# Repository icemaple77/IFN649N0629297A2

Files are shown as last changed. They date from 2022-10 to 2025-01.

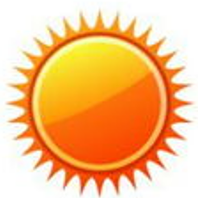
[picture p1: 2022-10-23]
layer3/client/src/img/sunny.png

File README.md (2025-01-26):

# Secure Cloud Infrastructure for Enterprise

## **Introduction**

This project mainly realized a fully automatic, unattended, green energy irrigation system. Firstly, the system is mainly divided into three layers and four modules, which are sensor layer, edge computing layer and cloud layer. The modules are data processing module, instruction management module, power management module and visualization module.

The system is powered by solar panels, and electric energy is stored into an 18650 storage battery through a 12-volt to 5-volt three-terminal voltage regulator. The sensor and MCU are powered by the battery. If the unsunny or less sunny area provides a 5V charging interface, a mobile phone charger can be used to power the entire system. The data detected by the sensor will be sent to the Raspberry PI in the middle layer, which will simply process the received data and publish the data to the AWS MQTT server for use by other clients. At the same time, a nano pi will subscribe to the data from the cloud, detect whether the data has changed, and send the latest value to the monitor for display. The watering controller controls the pump to complete the automatic irrigation according to the change of the value. This action can also be controlled by the user via an APP.

At the same time, a Web Server is set up on AWS to provide users with visual data access.

### **Keywords: MQTT, IoT, Network, Solar, Raspberry Pi, Water Pump,irrigation, Python, Arduino, Nodejs, AWS,Mosquito, Express, react， C， C++，Teensy，**

## **Example: [https://www.chenyun.org](https://www.chenyun.org/)**

## **Directory**



There are three project directories, one for each level of Code.

layer 1: Arduino Code.

layer 2: Js and python code (Python code to be perfected)

layer 3: Express Sever and React Client



The key used system directory corresponds to

Sensor

Pump

Monitor

Each directory contains the system firmware for an Arduino, and the applicable version is Teensy 2.0

The Arduino kit can be used to brush the hardware, and the link diagram is introduced later.



The Node file used in this example lives in the Node directory and is running under Node16.0. Simply execute node + file.js on a machine with a network connection.

`node Sensor.js`

`node Pump.js`

`node Monitor.js`

Make sure the teensy device has a Bluetooth connection to the device you're running the app on before executing the command.



The Server should be deployed on a Linux server with Node js 16.0 installed.

The command is

`cd Server`

`Npm install`

`npm start`

## **Architecture**









## **Design circuit diagram**

[]()

### **Sensor**



### **Pump**



Monitor



### **Technical parameters**

Sensor:

1. Rain Sensor
2. Temperature and Humidity Sensor
3. Soil moisture Sensor
4. Teensy 2.0 board
5. 18650 battery
6. switch x 2
7. Led
8. 3 Pin Socket x 2
9. Charge Board
10. 12v to 5v Regulator
11. sink
12. Bluetooth HC-05

Pump:

1. Teensy 2.0 board
2. Bluetooth HC-05
3. PNP 140 Transistor
4. Water Pump

Monitor

1. Teensy 2.0 Board
2. 0.96 LCD
3. Bluetooth HC-05

Flow Diagram



Web





<!--TLS is used to encrypt the session transmission to ensure data security.-->


Be sure to replace your own CA certificate



Link:

MQTT:

mqtt://mqtt.chenyun.org

port: 1883

Username password authentication has been enabled



## **The power supply parameters**



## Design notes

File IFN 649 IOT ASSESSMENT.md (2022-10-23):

# IFN 649 IOT ASSESSMENT

## Introduction

This project mainly realized a fully automatic, unattended, green energy irrigation system. Firstly, the system is mainly divided into three layers and four modules, which are sensor layer, edge computing layer and cloud layer. The modules are data processing module, instruction management module, power management module and visualization module.

The system is powered by solar panels, and electric energy is stored into an 18650 storage battery through a 12-volt to 5-volt three-terminal voltage regulator. The sensor and MCU are powered by the battery. If the unsunny or less sunny area provides a 5V charging interface, a mobile phone charger can be used to power the entire system. The data detected by the sensor will be sent to the Raspberry PI in the middle layer, which will simply process the received data and publish the data to the AWS MQTT server for use by other clients. At the same time, a nano pi will subscribe to the data from the cloud, detect whether the data has changed, and send the latest value to the monitor for display. The watering controller controls the pump to complete the automatic irrigation according to the change of the value. This action can also be controlled by the user via an APP.

At the same time, a Web Server is set up on AWS to provide users with visual data access.

#####  Keywords: MQTT, IoT, Network, Solar, Raspberry Pi, Water Pump,irrigation, Python, Arduino, Nodejs, AWS,Mosquito, Express, react， C， C++，Teensy，

## Example: https://www.chenyun.org

## Directory



There are three project directories, one for each level of Code.

layer 1: Arduino Code.

layer 2: Js and python code (Python code to be perfected)

layer 3: Express Sever and React Client



The key used system directory corresponds to

Sensor

Pump

Monitor

Each directory contains the system firmware for an Arduino, and the applicable version is Teensy 2.0

The Arduino kit can be used to brush the hardware, and the link diagram is introduced later.



The Node file used in this example lives in the Node directory and is running under Node16.0. Simply execute node + file.js on a machine with a network connection.

`node Sensor.js`

`node Pump.js`

`node Monitor.js`

Make sure the teensy device has a Bluetooth connection to the device you're running the app on before executing the command.



The Server should be deployed on a Linux server with Node js 16.0 installed.

The command is

`cd Server`

`Npm install`

`npm start`

## Architecture









## Design circuit diagram

### Sensor



### Pump



Monitor



### Technical parameters

Sensor:

1. Rain Sensor
2. Temperature and Humidity Sensor
3. Soil moisture Sensor
4. Teensy 2.0 board
5. 18650 battery
6. switch x 2
7. Led 
8. 3 Pin Socket x 2
9. Charge Board
10. 12v to 5v Regulator
11. sink
12. Bluetooth HC-05

Pump:

1. Teensy 2.0 board
2. Bluetooth HC-05
3. PNP 140 Transistor
4. Water Pump

Monitor

1. Teensy 2.0 Board
2. 0.96 LCD
3. Bluetooth HC-05

Flow Diagram



Web





<!--TLS is used to encrypt the session transmission to ensure data security.-->





Be sure to replace your own CA certificate

Link:

MQTT: 

mqtt://mqtt.chenyun.org

port: 1883

Username password authentication has been enabled

	

## The power supply parameters



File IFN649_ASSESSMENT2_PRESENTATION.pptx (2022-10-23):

## IFN 649 Advanced Networks Assessment2 Smart watering system

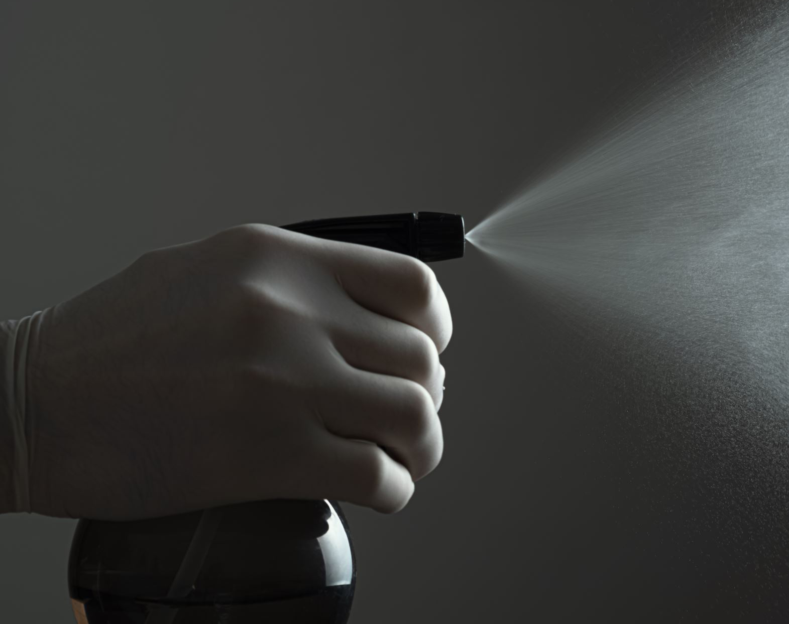
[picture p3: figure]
Hand spraying sanitiser

Lecturers: Prof Raja Jurdak
Dr. Gowri Ramachandran
Tutor name: Jun Wook Heo
Student ID： N10629297
Student Name： Chen Yun（Michael）

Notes:
For the project I‘m going talk about smart watering system

## Description of project

d

Tier 1： outdoor

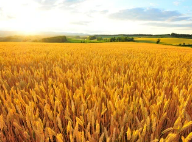
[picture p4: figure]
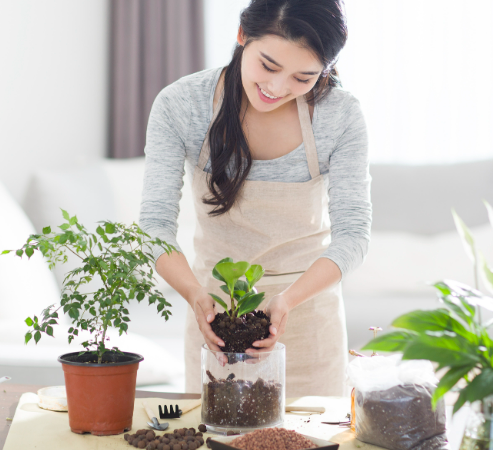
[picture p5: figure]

Internet

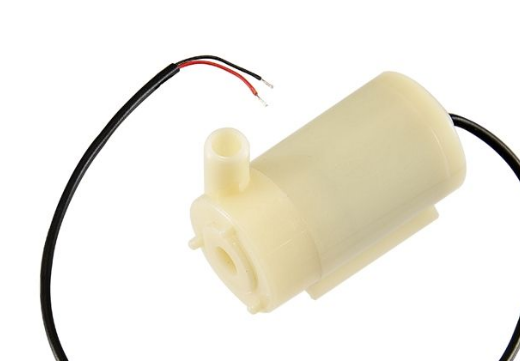
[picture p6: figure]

MCU

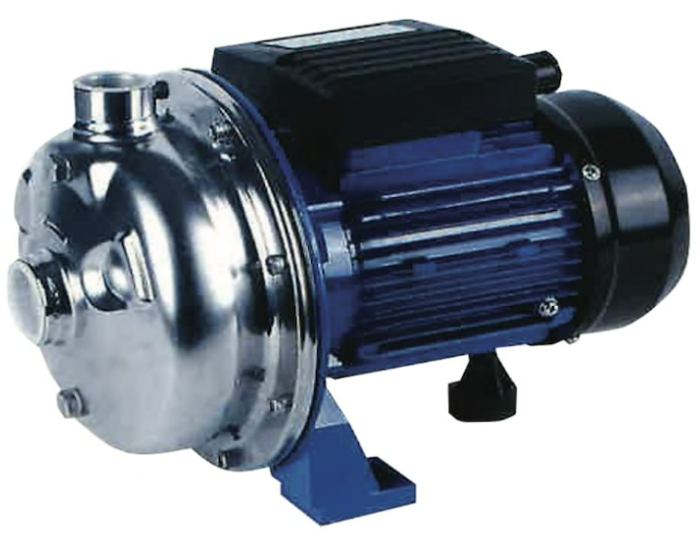
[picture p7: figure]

Tier 2

Essential: MQTT Server

Optional: Web Service

Tier 3

Rain sensor

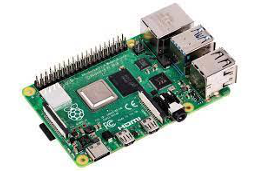
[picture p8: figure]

MCU

Temperature sensor

Soil moisture sensor

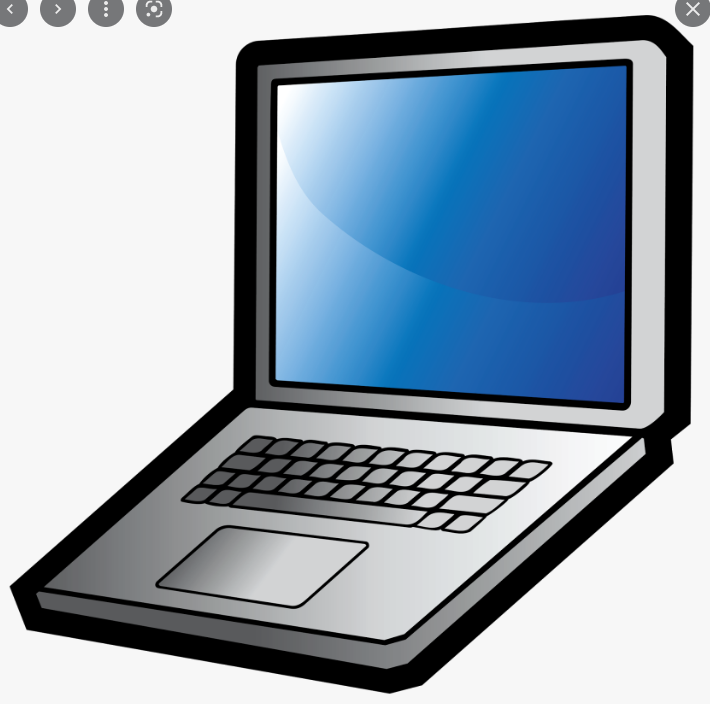
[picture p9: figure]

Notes: This project is mainly to address a problem of watering plants.
Different plants have different water requirements, and either leaving the water or overwatering will lead to the death of the plant.
And watering plants in hot or cold weather could lead to unhealthy for them
So using this system can help us to water the plants automatically.
As this diagram, the system include 3 layers.
Firstly, MCU is used to control some sensors in the first layer.
these sensors are mainly responsible for collect moisture data of soil, monitor the temperature of the environment and detect whether when it is raining.

the MCU is responsible for forwarding data to the second layer, or receiving order from the Raspberry PI to control the watering pump.

Next talk about the second layer, Raspberry PI exchanges data with first layer via Bluetooth.
At the here, I consider using wifi to replace Bluetooth, because WIFI can increase the distance and improve stability for transmission .
MQTT service will be used in this system . It is responsible to subscribe and publish data for Raspberry PI.
In addition, if I have enough time, I will build a web service based Nodejs to display the data on the web.
The detailed working principle of each layer will be introduced later.
。
The system can be used in many scenarios . For example, it can help farmers to water farm automatic.
Or at home it also can be used to water plant in the yard.
It can help people to save time and save water. The important is that it can keep the plants living healthy
Next, I will talk about each layer how does it work

## Sensor layer

Tier 2

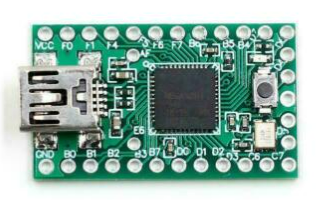
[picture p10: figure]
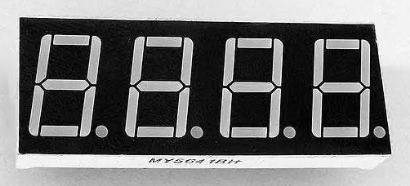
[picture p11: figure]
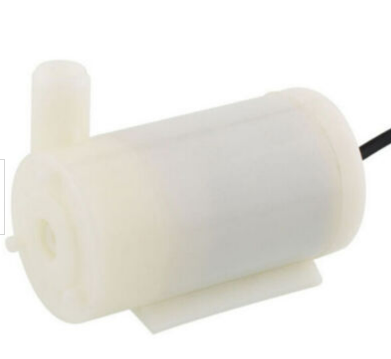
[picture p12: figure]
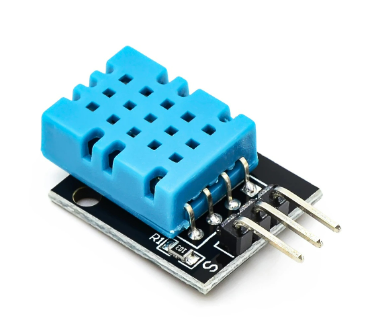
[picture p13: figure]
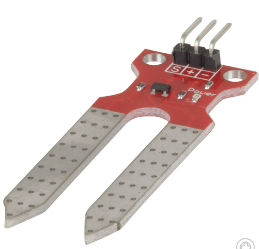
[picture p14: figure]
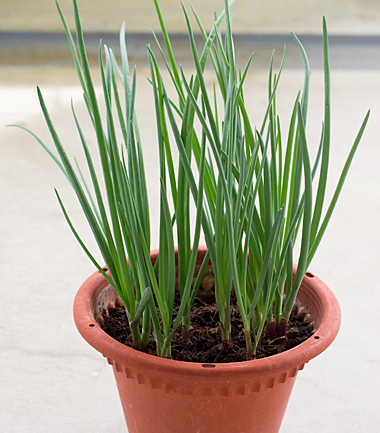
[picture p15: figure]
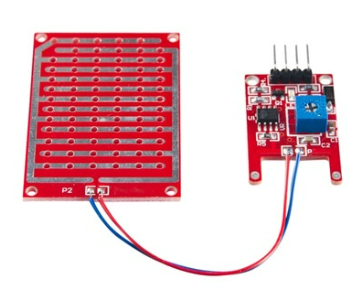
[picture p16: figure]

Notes: The first layer is sensor layer
There are three sensors used here and a water pump
The value of moisture will be got through the soil sensor
The rain sensor detects if it’s raining
The temperature sensor get the temperature from the environment
Digital tube display the value of soil moisture
Mcu can be used to send these data to the second layer or get the order from that to control the water pump

Temperature level will be considered
That means when the temperature is too high or too low, no water command is sent
Because it's bad for the health of the plant, when water a plant in the hot or cold wether
And When the raining, it will be stopped to monitor the soil sensors.

## Edge Tier

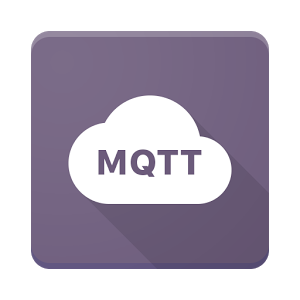
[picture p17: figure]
Minimal MQTT: Control And Clients | Hackaday

MQTT Client running in Raspberry Pi (Linux OS)
Using a Script of Python to Sub & Pub message
Retrieve and Send data from or to Teensy by BT

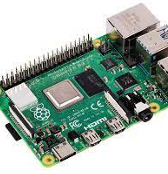
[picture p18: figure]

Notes: The second layer is edge layer
Because there is a Linux operation system will be runing on Raspberry PI, we can do a lot of things
Firstly, the second layer mainly response to process the data of first layer and give an order to first layer
Then, it will publish the data to the cloud
In this case, publishing data to the cloud will use MQTT or Socket
The connection to the first layer could use Bluetooth or wifi for data transmission
using Python to program a application to process the data
For Examples temperature determination, rain detection, and soil moisture detection.
The application also needs to give orders to the pump when the plant needs to be watered.同时还要判断是否达到浇水的条件给水泵的控制器下发指令。

## Cloud tier

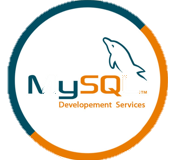
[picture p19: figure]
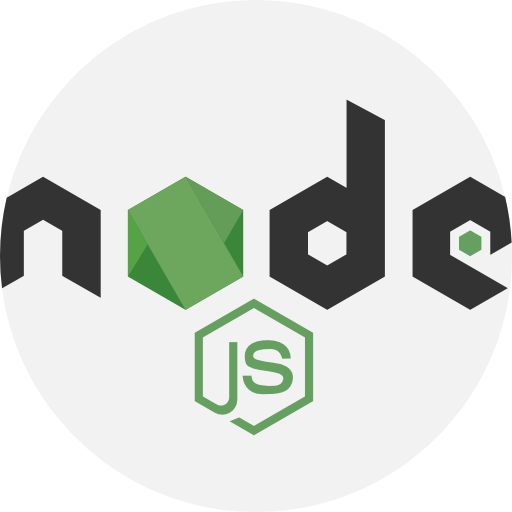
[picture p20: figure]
Nodejs - Free brands and logotypes icons

MQTT Server
An MQTT server is run to provide data forwarding services for the clients in the second layer

Web Server
Create a Web service and subscribe to the messages published by the tier 2 client and display them on the page

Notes: In the third layer of cloud,
it is mainly to provide some persistent services
First of all, it is necessary to deploy the MQTT server. The MQTT server is developed based on Socket and uses TCP/IP protocol for data transmission,
so that it has a the reliability for transmission data

Then I could use Express to build a server that can visualize the data to the user.
Users can use mobile phones or laptops to access websites to browser data, or click a button to control the sensor.

## Consideration

Salary panel

12Volt
100-180mA

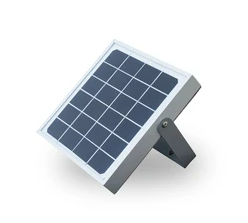
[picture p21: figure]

X4

Power

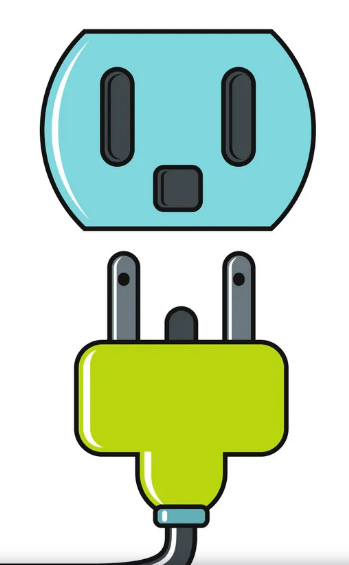
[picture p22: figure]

Power analysis
Supply:
12V & 400-800mA
Charge in 5-8 hours
Requirement：
Total：
Approximately 100mA
Use continuously for 26 hours

5V DC Converter

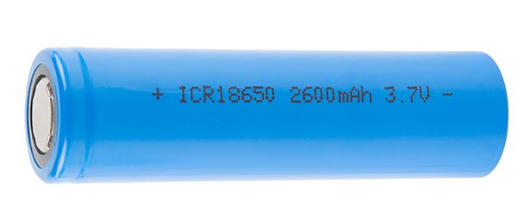
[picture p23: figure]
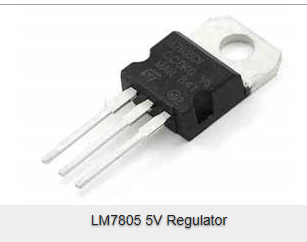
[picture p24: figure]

LM7805 voltage regulator

18650 battery
3.7 volt
26000mAH

| Teensy | BlueTooth | Sensors
Power(W)
Voltage(V) | 5V | 3.3V | 3.3V
electric current(mA) | 10-30mA | 40mA-50mA | 4mA-10mA(per)

15 Watts

5 Volt

3 Ampere

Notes: For this section, I mainly consider the power and security , because some devices I borrowed from Uni, that means I couldn‘t put them into a sealed plastic box.

For the power ,In this case. I will use the socket for the raspberry pi. Because it need 15 watts of power. But I will use the salary energy to supply the power to first layer.
I am very luck , I found one Salary panel from rubbish-bin and it does work,
then I get a voltage regulator from the Uni , it can change the voltage from 12 to 5
And I have measured the power consumption of all the devices
After calculation, use a battery to private the power can ensure the sensors with teensy working more than 20 hours.
And if I have 4 salary panels ,just need 5-8 hours ,the battery can be charged completely.
Even though I only have one solar panel, the whole system also works.
Therefor the power problem has been addressed, the system can be portable

## Consideration

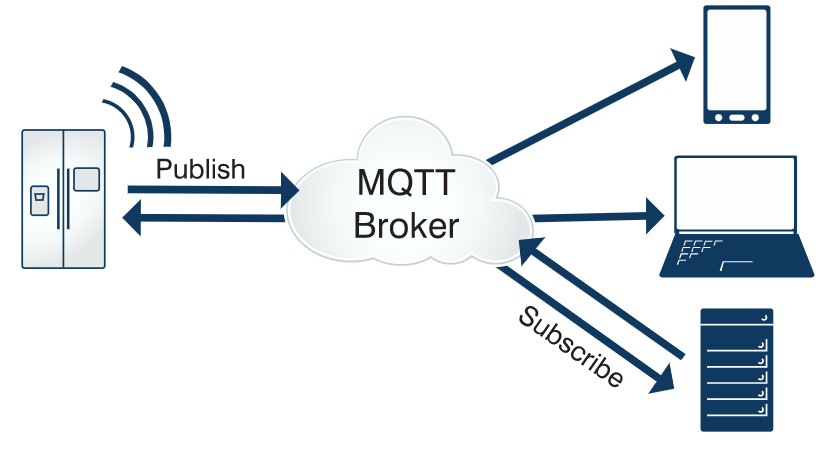
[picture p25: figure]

- Security
  - Devices Security
Set a specific KEY in MCU
  - Network Security
config /etc/mosquitto/mosquitto.conf
disable the allow_anonymous
  - Data Security
Using AWS-MySQL to storage the data
- Cost
Total : 90 AUD in AU, but only 20 AUD in China (not include Raspberry Pi)

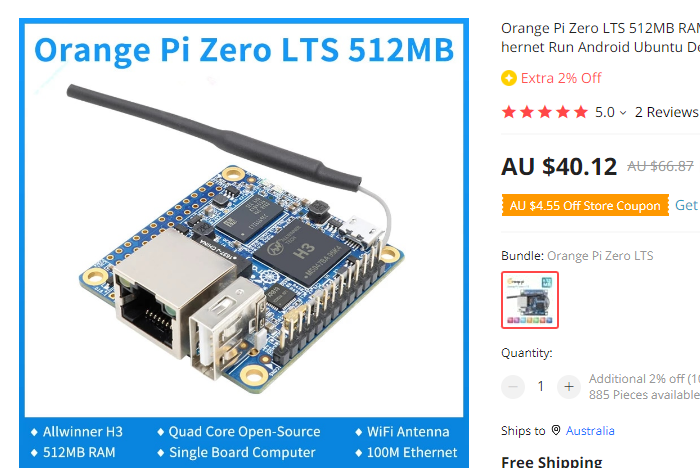
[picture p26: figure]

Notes: For Security section, I can set a key when I program the code for Arduino ,and the sensors only can be turned on or off by getting correct message
After that ,I have to disable no useful port of Linux on raspberry pi and config the ssh connection module must be used the private key
and config the MQTT service to verify the username and password
Lastly for the data parts I could use the MySQL with AWS to storage the sensitive data
For the totally cost ,I have spent 90 dollar to buy these devices from jaycar.It’s so expensive
Because if I buy them on Chinese online markets ,only less than 20 dollar is enough .
And for Raspberry pi , I don’t consider this device
because a chip that can run Linux could replace the Raspberry PI, Such as Orange Pi，I often use it as a Linux platform to develop some application . It offers the same functionality as Raspberry PI, but cheaper than that.

## Methodology

Research Method

Artefact-oriented research method

The final purpose of this project is that an intelligent watering completion system can be implemented, which can accept the user's command switch, and the system is portable. The unattended mode can make the system run continuously without any intervention to ensure the growth of the plant.

Research Structure

Propose
- Specify a project goal to accomplish, which is already set in this case. Implement an intelligent watering system

Plan & Design
- Develop execution plan and backup plan. Fully consider the problems that may occur in the project and look for solutions.

Collect and evaluate the equipment
- Collect the equipment in the project and test it
- Evaluate whether its functionality meets the requirements of the project

Experiment
- Connect the device according to the designed circuit diagram
- Write the code
- Deploy the service

Test
Test the operation of the whole system under different conditions.

Delivery
Deliver and demonstrate the entire system

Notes:
this is my schedule for this project.
Because I have already done the first three parts so I will try to connect the devices like sensors from this week and programming in the next week .
So I think I can complete the whole project before the due date.

## Thank you

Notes: That’s all
Thank you!

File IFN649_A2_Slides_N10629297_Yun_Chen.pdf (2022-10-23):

# IFN 649 Advanced


# Networks Assessment2 Smart watering system

Lecturers: | Prof Raja Jurdak
| Dr. Gowri Ramachandran
Tutor name: | Jun Wook Heo
Student ID： | N10629297
Student Name： | Chen Yun（Michael）

# Description of project

## Internet


d

Soil moisture
sensor

MCU

Tier 1： outdoor

Rain sensor

Temperature
sensor

Tier 2

MCU

Tier 3

Essential: MQTT Server
Optional: Web Service

Sensor layer | Tier 2


# Edge Tier


MQTT Client
running in
Raspberry Pi (Linux

Using a Script of
Python to Sub &
Pub message

Retrieve and Send
data from or to
Teensy by BT

# Cloud tier


## MQTT Server

An MQTT server is run
to provide data
forwarding services
for the clients in the
second layer

## Web Server

Create a Web service
and subscribe to the
messages published
by the tier 2 client
and display them on
the page

# Consideration

## Power


15 Watts
5 Volt
3 Ampere
| Teensy | BlueTooth | Sensors
Power(W)
Voltage(V) | 5V | 3.3V | 3.3V
electric current(mA) | 10-30mA | 40mA-50mA | 4mA-10mA(per)

12Volt
100-180mA

## Salary panel

LM7805 voltage
regulator

18650 battery
3.7 volt
26000mAH

X4

5V DC Converter

## Power analysis

## Supply:

12V & 400-800mA
Charge in 5-8 hours

## Requirement： Total：

Approximately 100mA
Use continuously for 26 hours

# Consideration


## - Security

- Devices Security
Set a specific KEY in MCU
- Network Security
config /etc/mosquitto/mosquitto.conf disable the allow_anonymous
- Data Security
Using AWS-MySQL to storage the data

## - Cost Total : 90 AUD in AU, but only 20 AUD in China (not include Raspberry Pi)

# Methodology

Research Method | Artefact-oriented research method

Research Structure

The final purpose of this project is that an intelligent watering completion system can be implemented, which can accept the user's command switch, and the system is portable. The unattended mode can make the system run continuously without any intervention to ensure the growth of the plant.

Propose

- Specify a project goal
to accomplish, which is
already set in this case.
Implement an
intelligent watering
system

Plan & Design

- Develop execution
plan and backup plan.
Fully consider the
problems that may
occur in the project
and look for solutions.

Collect and evaluate
the equipment
- Collect the equipment in the project and test it
- Evaluate whether its
functionality meets the
requirements of the
project

Experiment

- Connect the device
according to the designed
circuit diagram
- Write the code
- Deploy the service

Test

Test the operation of the
whole system under different conditions.

Delivery

Deliver and demonstrate
the entire system

Thank you

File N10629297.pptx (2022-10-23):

## IoT

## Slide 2


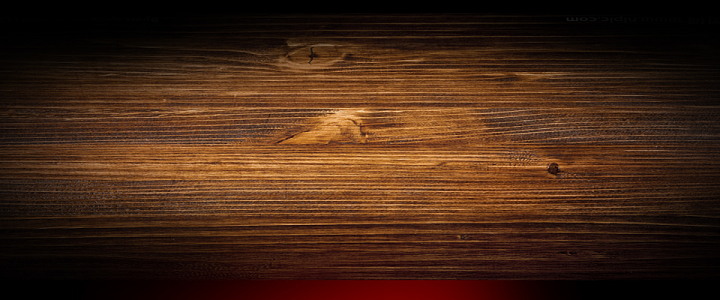
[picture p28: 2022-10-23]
d732e8a6_E823042_5aef47e3.jpg

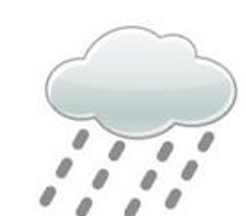
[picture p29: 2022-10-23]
layer3/client/src/img/rainy.png

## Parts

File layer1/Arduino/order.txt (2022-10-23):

String comdata = "";
void setup()
{
  Serial.begin(9600);
  for(int i = 2; i <= 13; i++) pinMode(i, OUTPUT);
}

void loop()
{
  while (Serial.available() > 0)
  {
    comdata += int(Serial.read()) - '0';
    delay(2);
  }
  if(comdata.length() > 0)
  {
    for(int i = 0; i < comdata.length(); i++)
    {
      if(comdata[i]=='0'||comdata[i]=='1')
      {
        digitalWrite(i + 2, comdata[i] - '0');
        Serial.print("Pin ");
        Serial.print(i + 2);
        Serial.print(" is ");
        Serial.println(comdata[i]);
      }
    }
    comdata = "";
  }
}

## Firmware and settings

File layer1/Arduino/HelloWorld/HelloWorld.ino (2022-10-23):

#include "U8glib.h"
#define LEDPIN 11
#define rxPin 7 // Teensy pin 7 <--> HC-05 Tx
#define txPin 8 // Teensy pin 8 <--> HC-05 Rx
int mark;
int p;
int strIndex = 0;
int x=4;
int y=18;
int sub_x=4;
int sub_y=38;
String *fString[4];
String date="2022-09-28";
String temperature="Centigrade: 25";
String soil="Moist";
String info="Sunny day";
String comdata;
void pageTimeDay();     // Page-1
void pageTemperature(); // Page-2
void pageHumidity();    // Page-3
void pageInfo();        // Page-4

void (*pages[])() = { pageTimeDay, pageTemperature, pageHumidity, pageInfo } ;
U8GLIB_SSD1306_ADAFRUIT_128X64 u8g(10, 9, 4, 5, 6);
//U8GLIB_SSD1306_128X64 u8g(10, 9, 13, 12, 14);  // SW SPI Com: SCK = 13, MOSI = 11, CS = 10, A0 = 9
void draw(void) {
  // graphic commands to redraw the complete screen should be placed here  
  u8g.setFont(u8g_font_unifont);
  //u8g.setFont(u8g_font_osb21);
  u8g.drawStr( 1, 22, "Hello Stone!");
}

void setup(void) {
  // flip screen, if required
  // u8g.setRot180();
  
  // set SPI backup if required
  //u8g.setHardwareBackup(u8g_backup_avr_spi);

  // assign default color value
  if ( u8g.getMode() == U8G_MODE_R3G3B2 ) {
    u8g.setColorIndex(255);     // white
  }
  else if ( u8g.getMode() == U8G_MODE_GRAY2BIT ) {
    u8g.setColorIndex(3);         // max intensity
  }
  else if ( u8g.getMode() == U8G_MODE_BW ) {
    u8g.setColorIndex(1);         // pixel on
  }
  else if ( u8g.getMode() == U8G_MODE_HICOLOR ) {
    u8g.setHiColorByRGB(255,255,255);
  }
  Serial.begin(9600);
  Serial1.begin(9600);
  digitalWrite(LEDPIN, HIGH);
  u8g.setFont(u8g_font_unifont);
  //u8g.setFont(u8g_font_8x13B);
  //u8g.setColorIndex(1);
  p = 0;
  fString[0] = &date;
  fString[1] = &temperature;
  fString[2] = &soil;
  fString[3] = &info;
  pinMode(11, OUTPUT);
}

void loop(void) {
  while (Serial1.available() > 0)//||Serial.available() > 0
    {
      comdata += char(Serial1.read());
      //comdata += char(Serial.read());
      mark=1;
    }
    delay(1000);
    if (mark==1)
    {
      Serial.println("=======================");
      date="";
      temperature="";
      soil="";
      info="";
      byte i;
      for (i=0; i<4; i++)
        *fString[i] = splitStr(comdata);
      Serial.println(comdata);
      for (i=0; i<4; i++)
        Serial.println(*fString[i]);
      mark=0;
      comdata="";
      strIndex = 0;
      delay(1000);
    }
  u8g.firstPage();
  do {  
    (*pages[p])();
  } while( u8g.nextPage() );
  delay(1000); 
  p = p+1;
  if (p == 4)
    p=0;
  

}
String splitStr(String str)
{
  if (strIndex == -1)
    return "";
  byte i = str.indexOf('^',strIndex)+1;
  strIndex = str.indexOf('^',i);
  if (strIndex == -1)
    return "";
  else
    return comdata.substring(i,strIndex);
}
void pageTimeDay() {
  u8g.drawStr( x, y, "Date of today:");
  u8g.setPrintPos(sub_x, sub_y);
  u8g.print(date);
  u8g.drawStr( x, 58, "Have a nice day");  
}
void pageTemperature(){
  u8g.drawStr( x, y, "Temperature:");
  u8g.setPrintPos(sub_x, sub_y);
  u8g.print(temperature);
}
void pageHumidity() {
  u8g.drawStr( x, y, "Soil Moisture:");
  u8g.setPrintPos(sub_x, sub_y);
  u8g.print(soil);
}
void pageInfo(){
  u8g.drawStr( x, y, "Weather:");
  u8g.setPrintPos(sub_x, sub_y);
  u8g.print(info);
}

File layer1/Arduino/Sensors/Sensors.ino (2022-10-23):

#include "DHT.h"
//#include <SoftwareSerial.h>

#define DHTPIN 12      // Digital pin connected to the DHT sensor
#define DHTTYPE DHT11   // DHT 11
#define RAINPIN 16 
#define LEDPIN 11
#define SOILPIN 21
DHT dht(DHTPIN, DHTTYPE);

class Sensor{
  private:
  int _pin;
  public:
  Sensor(int pin){
    _pin = pin;
  }
  int readValue(){
    return analogRead(_pin);
  }
};
float soilData() {
  float moisture_percentage;
  int sensor_analog;
  sensor_analog = analogRead(SOILPIN);
  moisture_percentage = ( 100 - ( (sensor_analog/1023.00) * 100 ) );
  return moisture_percentage;
  };
Sensor rain(RAINPIN);
Sensor soil(SOILPIN);
// Teensy 5V <--> HC-05 Vcc
// Teensy Ground <--> HC-05 GND
#define rxPin 7 // Teensy pin 7 <--> HC-05 Tx
#define txPin 8 // Teensy pin 8 <--> HC-05 Rx

int Mark=0; 
void setup() {
  // Setup serial for monitor
  Serial.begin(9600); 

  // Setup DHT Sensor
  pinMode(DHTPIN, INPUT);
  pinMode(LEDPIN, OUTPUT);
  pinMode(SOILPIN, INPUT);
  pinMode(RAINPIN, INPUT);
  dht.begin();
  digitalWrite(LEDPIN, HIGH);
  // Setup Serial1 for BlueTooth
  Serial1.begin(9600); // Default communication rate of the Bluetooth module
}

void loop() {
  if(Serial1.available() >0 || Serial.available() >0){ 
    String passwd=Serial1.readStringUntil('?');
    Serial.println(passwd);
    if(passwd=="Start"){
      Serial.println("Success Login");
      Serial1.println("Success Login");
      Mark=1;
      }
      else{
        Mark=0;
        Serial.println("Passwd is wrong");
        Serial1.println("Passwd is wrong");
        }
    }// Checks whether data is comming from the serial port  
  if (Mark==1){
    digitalWrite(LEDPIN, HIGH);    
    float h = dht.readHumidity();
    float t = dht.readTemperature();
    float s = soilData();
    int r = rain.readValue();
    Serial.print(F("Weather:"));
    Serial.print(r);
    Serial.print(F(","));
    Serial.print(F("Humidity:"));
    Serial.print(h);
    Serial.print(F(","));
    Serial.print(F("Temperature:"));
    Serial.print(t);
    Serial.print(F(","));
    Serial.print(F("Moisture:"));
    Serial.println(s);

    Serial1.print(F("Weather:"));
    Serial1.print(r);
    Serial1.print(F(","));
    Serial1.print(F("Humidity:"));
    Serial1.print(h);
    Serial1.print(F(","));
    Serial1.print(F("Temperature:"));
    Serial1.print(t);
    Serial1.print(F(","));
    Serial1.print(F("Moisture:"));
    Serial1.println(s);

    
    digitalWrite(LEDPIN, LOW);
    delay(5000);
    }  

 
}

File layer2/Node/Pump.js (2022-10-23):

const mqtt = require("mqtt");
const options = {
  // Clean session
  clean: true,
  //connectTimeout: 4000,
  // Auth
  clientId: "pump",
  username: "michael",
  password: "p19820301",
};
const client = mqtt.connect("mqtt://mqtt.chenyun.org", options);
const { SerialPort } = require("serialport");
const { ReadlineParser } = require("@serialport/parser-readline");
var moment = require("moment");

const mainTopic = "Pump";
const comm = "/dev/rfcomm1";
const config = { path: comm, baudRate: 9600 };
var order = "";
var voltage = "201";
var m_c = true,
  t_c = true,
  r_c = true,
  auto = true;

const port = new SerialPort(config, function (err) {
  if (err) {
    return console.log("Error: ", err.message);
  }
});

const parser = port.pipe(new ReadlineParser({ delimiter: "\r\n" }));
client.on("connect", function () {
  console.log("MQTT connected successful");
  // connected = client.connected
  client.subscribe(`Order/${mainTopic}`, { qos: 1 });
  client.subscribe(`Sensor/#`, { qos: 1 }); //订阅主题为test的消息
});
client.on("message", function (top, message) {
  //console.log("Topic:", top);
  //console.log("Value:", message.toString());
  let Msg = JSON.parse(message);
  if (top == "Order/Pump") {
    console.log(message.toString());
    order = Msg.order;
    auto = Boolean(Msg.auto);
  }
  if (auto == true) {
    //let tmp = JSON.parse(message);
    if (Msg.Topic == "Moisture") {
      if (Msg.Value < 20) m_c = true;
      if (Msg.Value > 40) m_c = false;
    }
    if (Msg.Topic == "Temperature") {
      if (Msg.Value > 4 || Msg.Value < 30) t_c = true;
      else t_c = true;
    }
    if (Msg.Topic == "isRaining") {
      if (Msg.Value == "0") r_c = true;
      else r_c = false;
    }
    if (m_c && t_c && r_c) order = "Start?" + voltage;
    else order = "Start?0";
    console.log(m_c, t_c, r_c);
  }
  const data = order.split("?");
  //console.log(data);
  if (data == "Start") Publish(order);
  else update(order);
});
function Publish(order) {
  update(order);
  parser.on("data", function (data) {
    console.log(data);
    if (data.Value != undefined) {
      client.publish(mainTopic, data.Value.toString(), {
        qos: 0,
        retain: true,
      });
      console.log("Public:", data);
    }
  });
}

function update(value) {
  port.write(value, function (err) {
    if (err) {
      return console.log("Error on write: ", err.message);
    }
    //console.log("Success ", value);
  });
}
